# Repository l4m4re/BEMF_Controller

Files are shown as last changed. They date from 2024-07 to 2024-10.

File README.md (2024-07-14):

# BEMF Controller

The Back EMF Controller is an experimental evolution of the successful [EasyController3](https://github.com/pgrady3/EasyController3). 

This version incorporates an asymmetric bridge topology, which allows for capturing and reusing the energy from the motor's back EMF, which is normally wasted because of the use of freewheeling diodes.

This allows for a more efficient controller, and potentially a longer range for battery-powered applications, as explained on [Wikipedia](https://en.wikipedia.org/wiki/Switched_reluctance_motor#Power_circuitry):

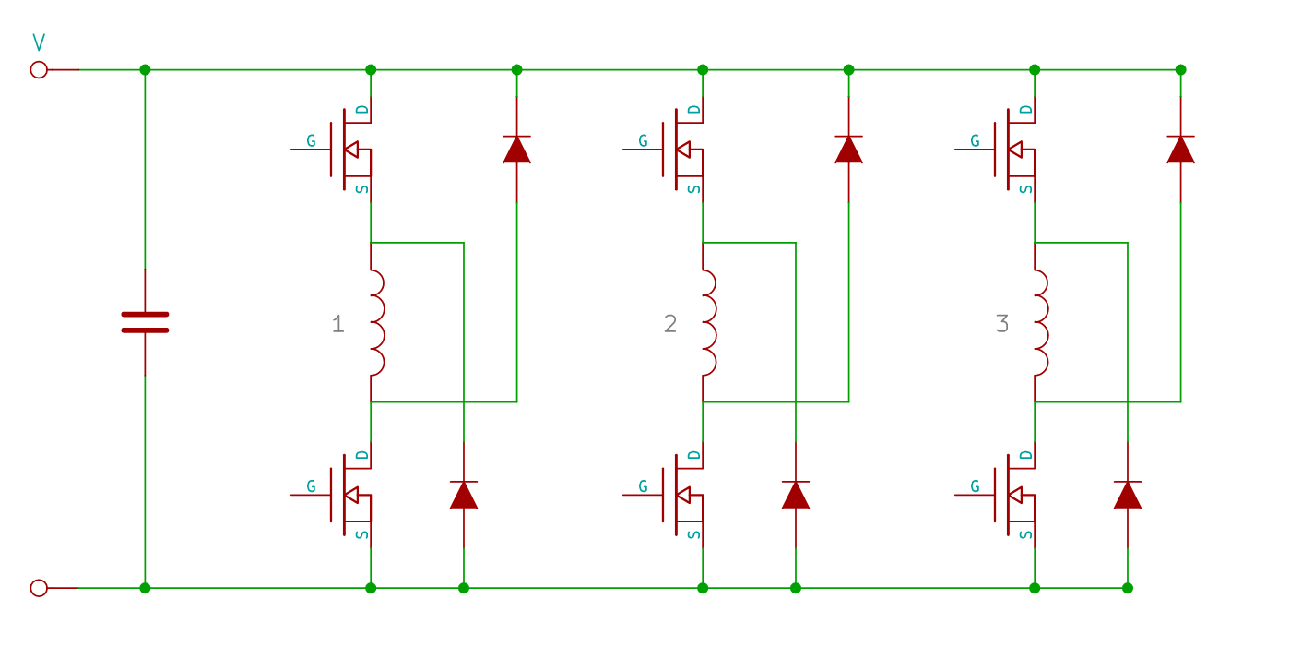
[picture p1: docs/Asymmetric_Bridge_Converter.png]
Asymmetric Bridge


> The phases in an asymmetric bridge converter correspond to the motor phases. If both of the power switches on either side of the phase are turned on, then that corresponding phase is actuated. Once the current has risen above the set value, the switch turns off. The energy now stored within the winding maintains the current in the same direction, the so-called back EMF (BEMF). This BEMF is fed back through the diodes to the capacitor for re-use, thus improving efficiency.

In addition to this, the capacitor that is used to store the energy from the back EMF is implemented in a bank of 4 capacitors, which are switched between series (BEMF capture) and parallel (coil energizing) by means of a couple of diodes:

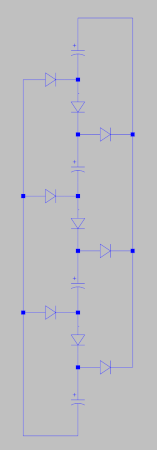
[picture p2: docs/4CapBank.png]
Capacitor Bank


[Spice simulations](http://tuks.nl/wiki/index.php/Main/BEMFRecoveryCircuit) have shown that this way the time needed to collapse the magnetic field in the motor is significantly reduced, which might help to reduce rotor drag and thus further improve the efficiency of the controller:

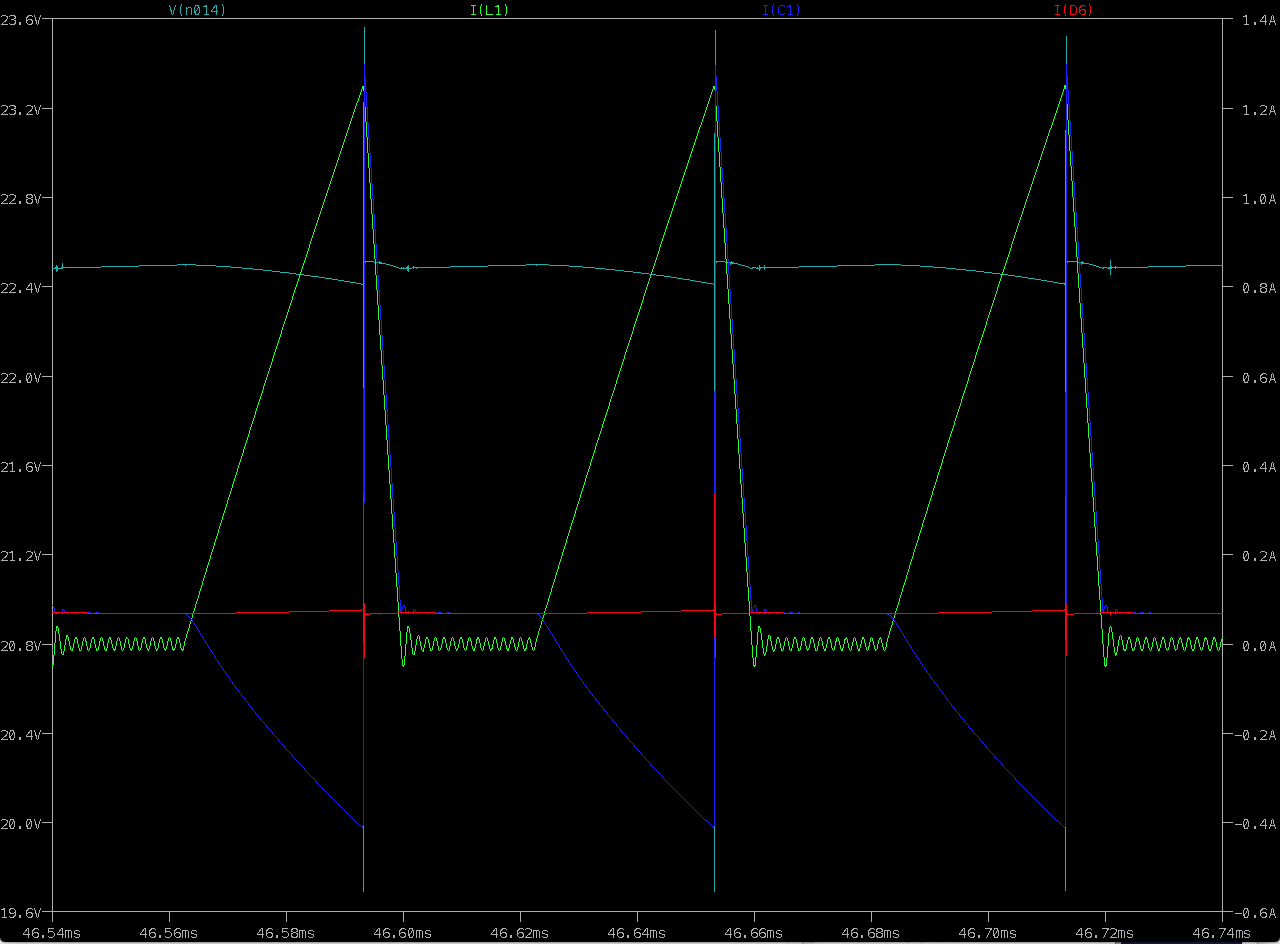
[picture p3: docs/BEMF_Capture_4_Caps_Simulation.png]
Spice simulation of 4 capacitor bank


At this moment, all of this is still a work in progress, and the controller is still in the design phase. 

## Schematic

At this moment, the schematic is being developed using KiCad, and can be found in the `kicad` folder. The schematic is still a work in progress, but the current version can be found [here](/kicad/BEMF_controller.pdf).

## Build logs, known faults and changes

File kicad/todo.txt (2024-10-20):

* Opamp buffers for Hall inputs -> check
* Finish buck converter -> check 
* Change gate drivers to LF2190NTR -> check
* Change trough hole resistors to smd -> check
* Change 10V charge pump to regulator
* Voltage sense now lower voltage and diodes no longer necessary since no cap switching
* Hall sensors could be DRV5055A3ELPGMQ1 https://www.digikey.nl/short/mpwrm95b 
* Connectors rather than pads -> ceck
* mounting holes
* check if inputs pen 1-4 can be used as digital inputs

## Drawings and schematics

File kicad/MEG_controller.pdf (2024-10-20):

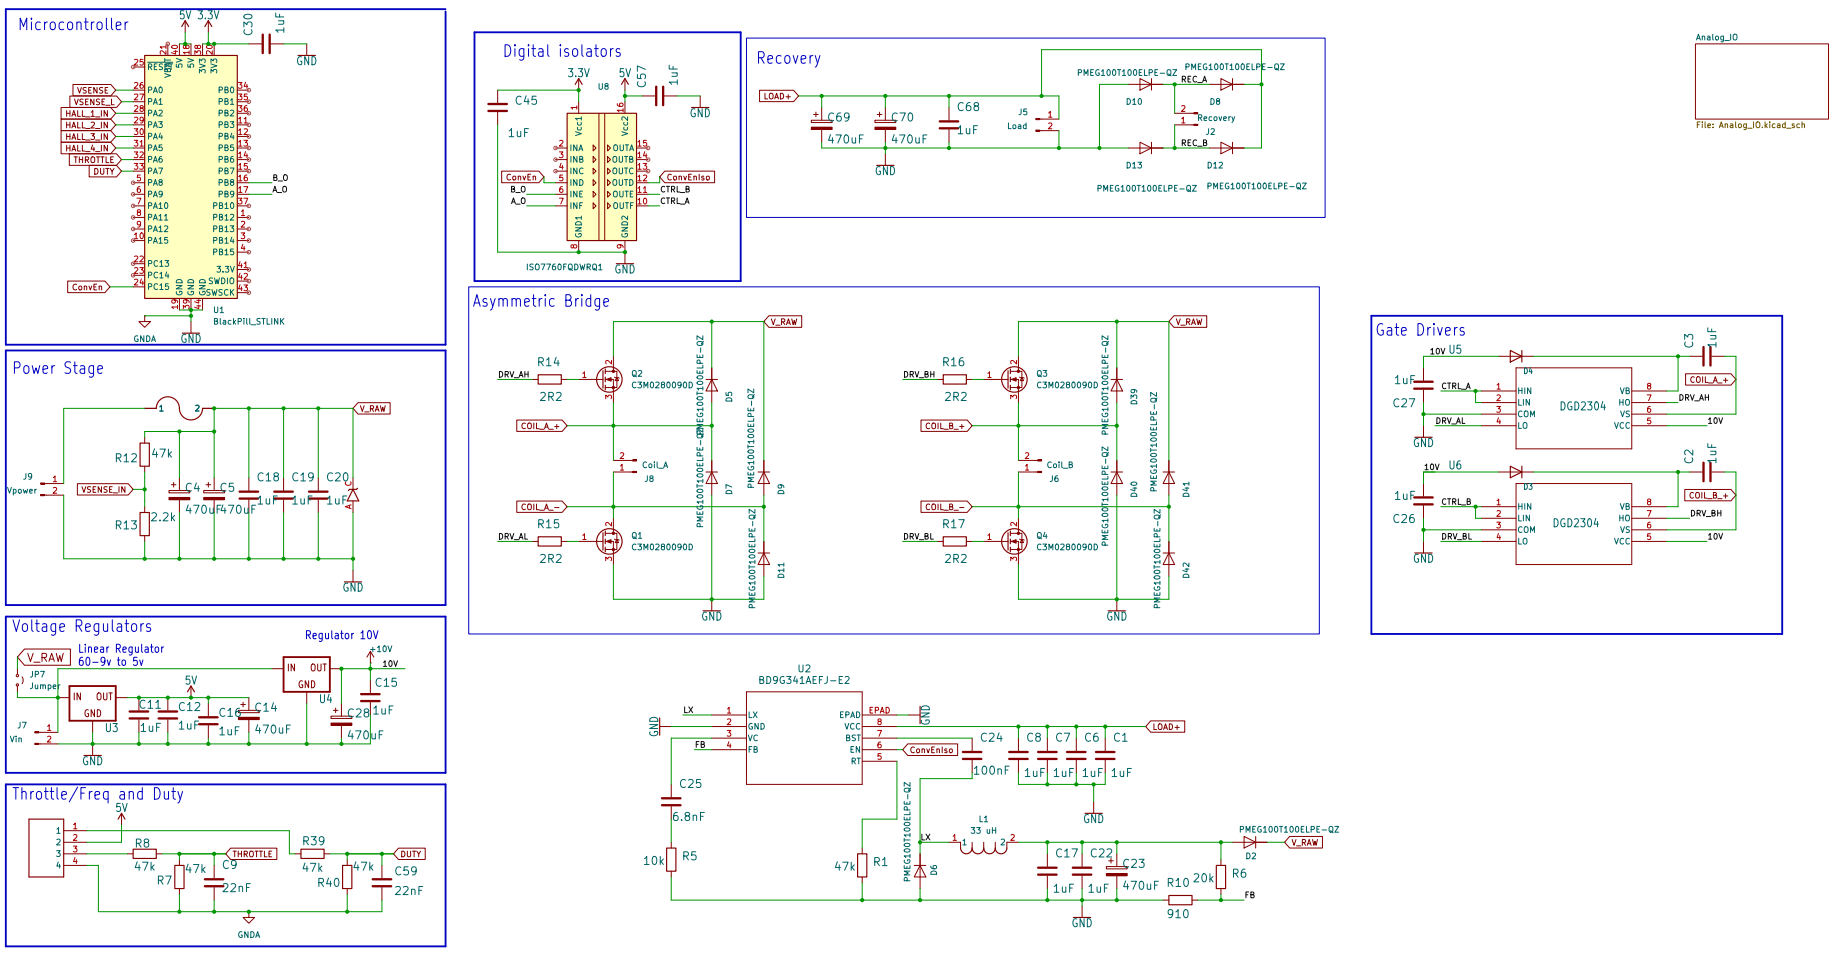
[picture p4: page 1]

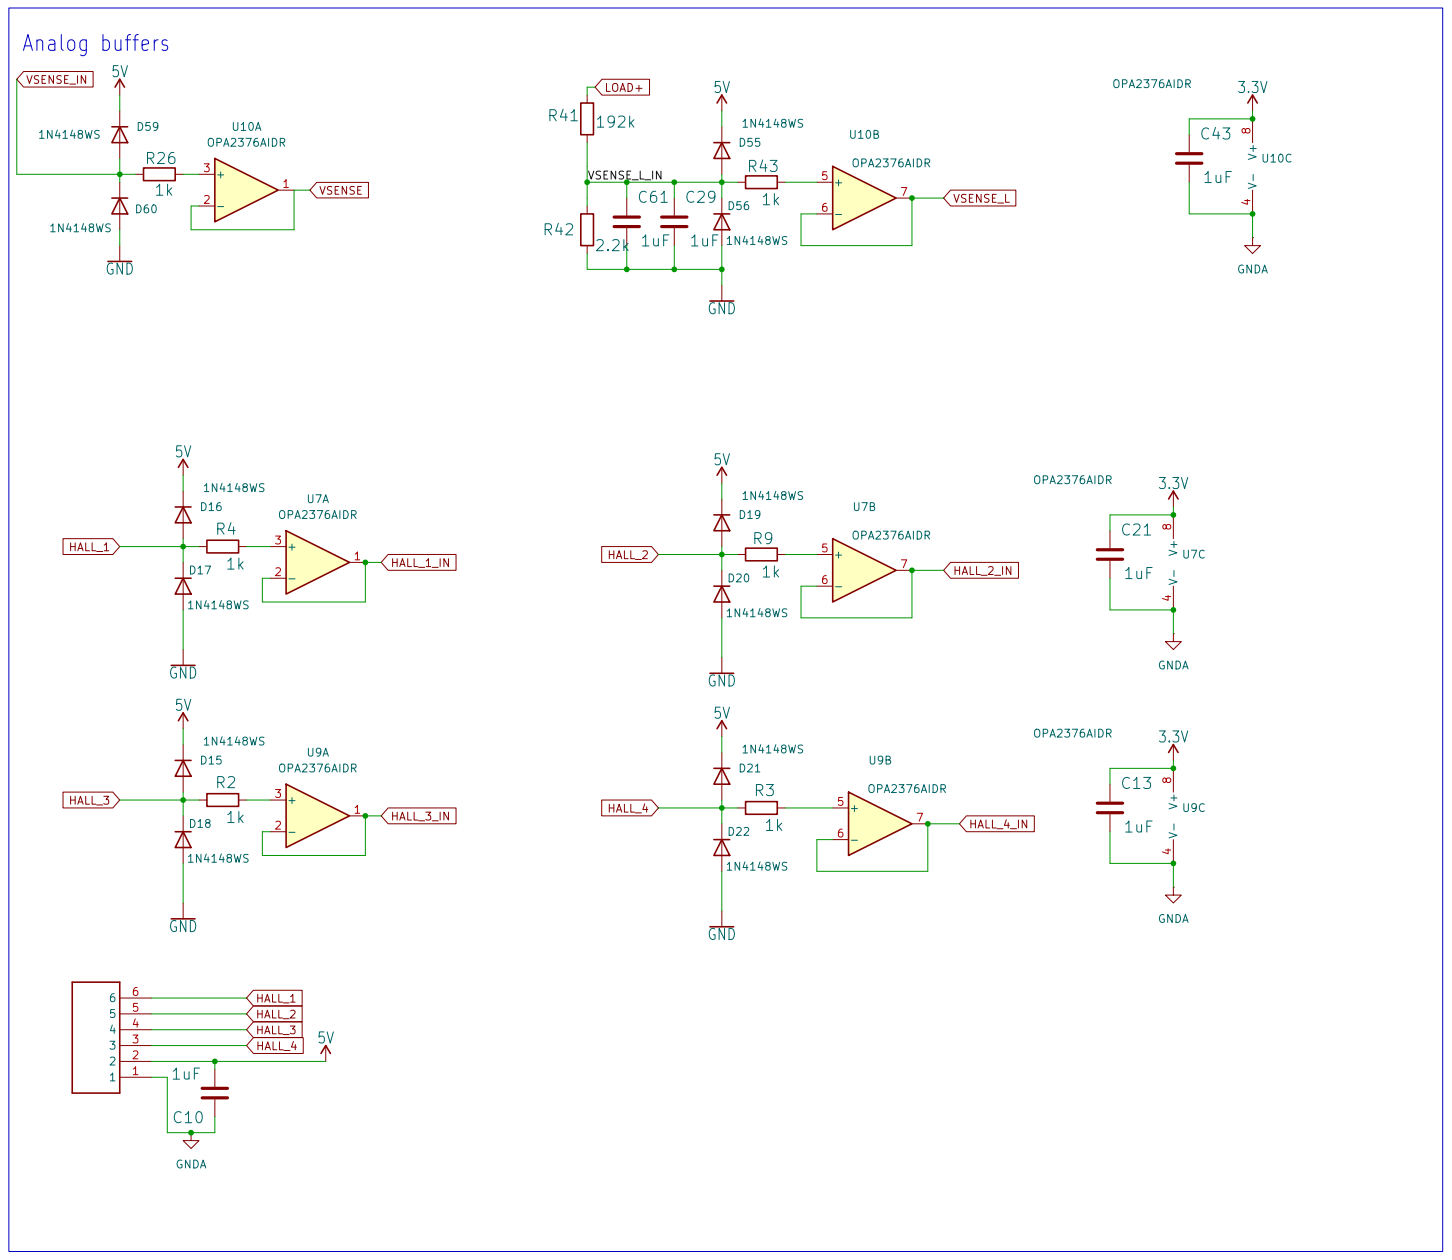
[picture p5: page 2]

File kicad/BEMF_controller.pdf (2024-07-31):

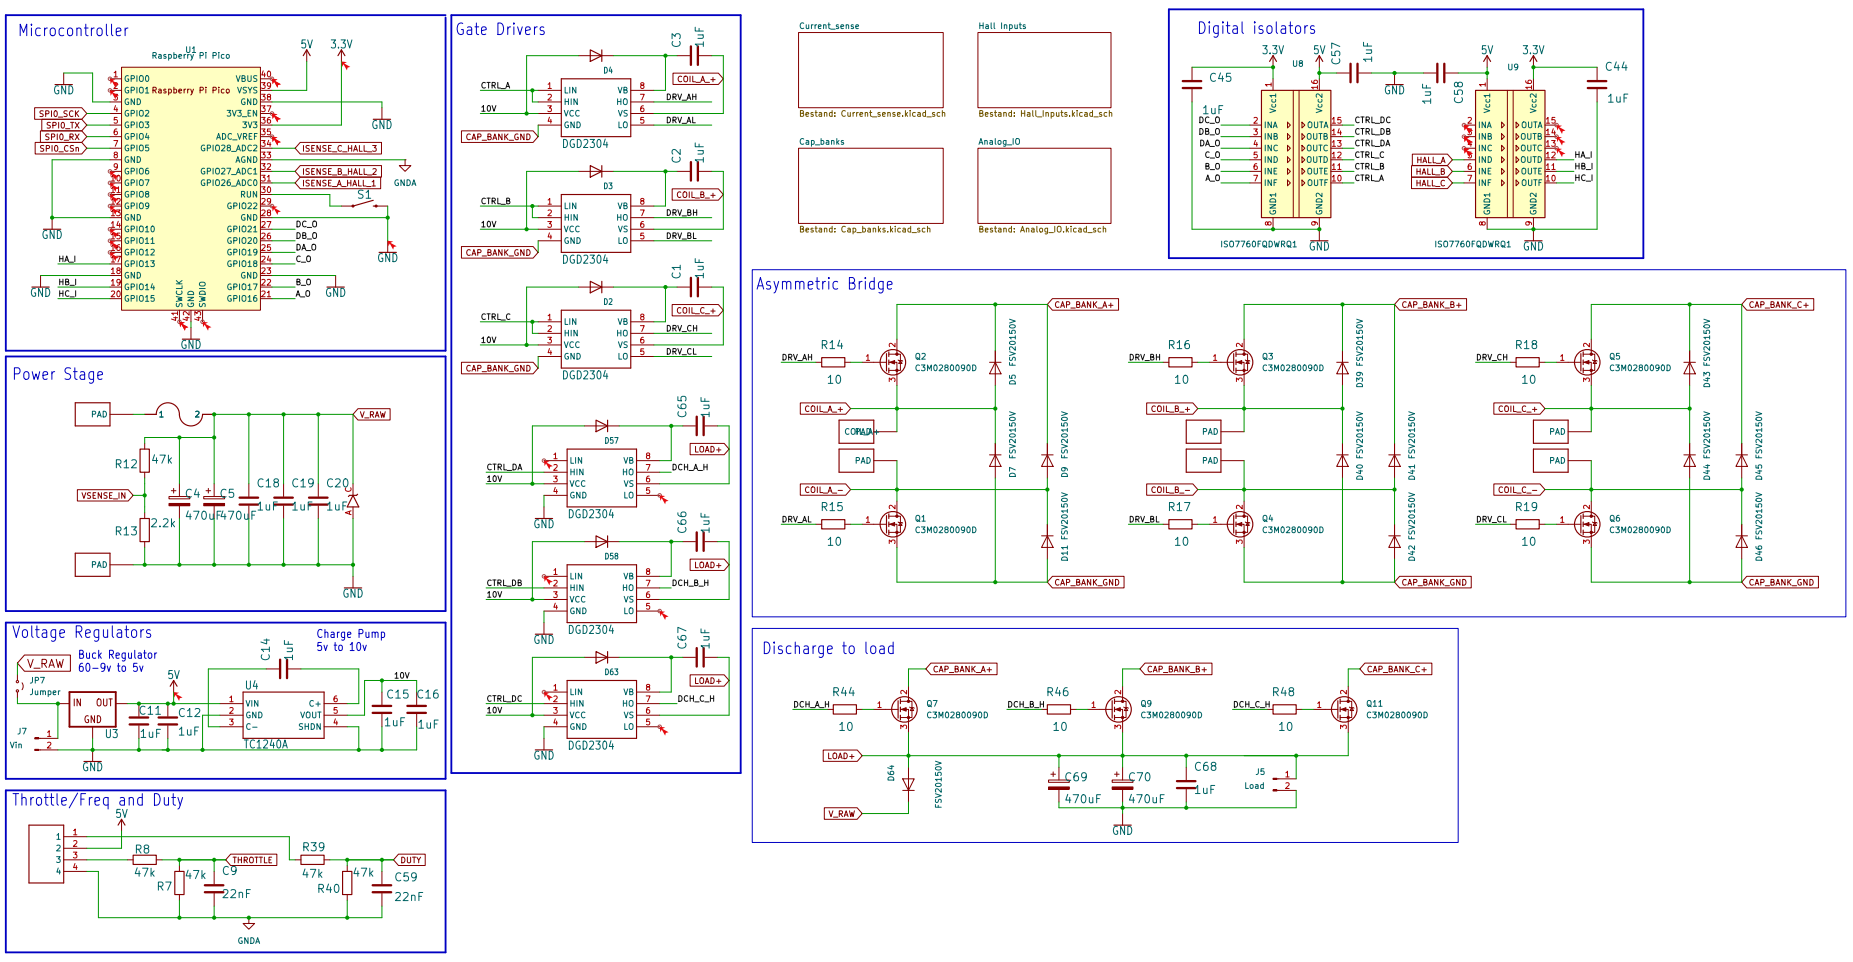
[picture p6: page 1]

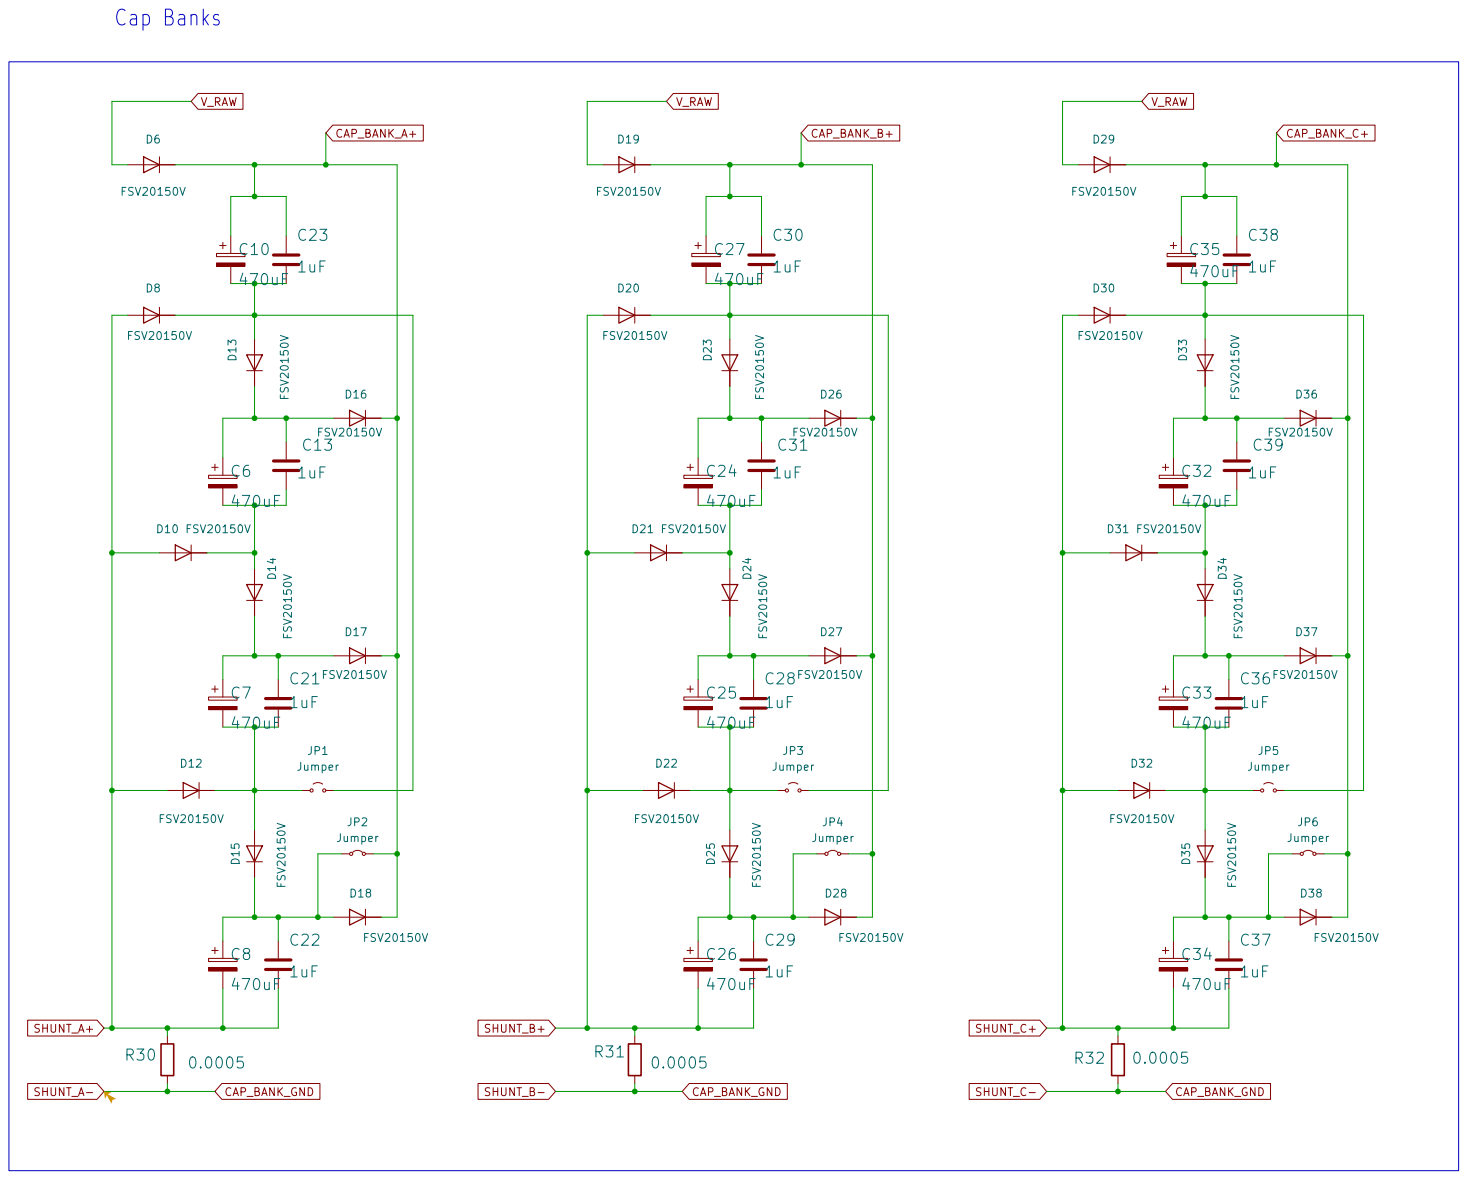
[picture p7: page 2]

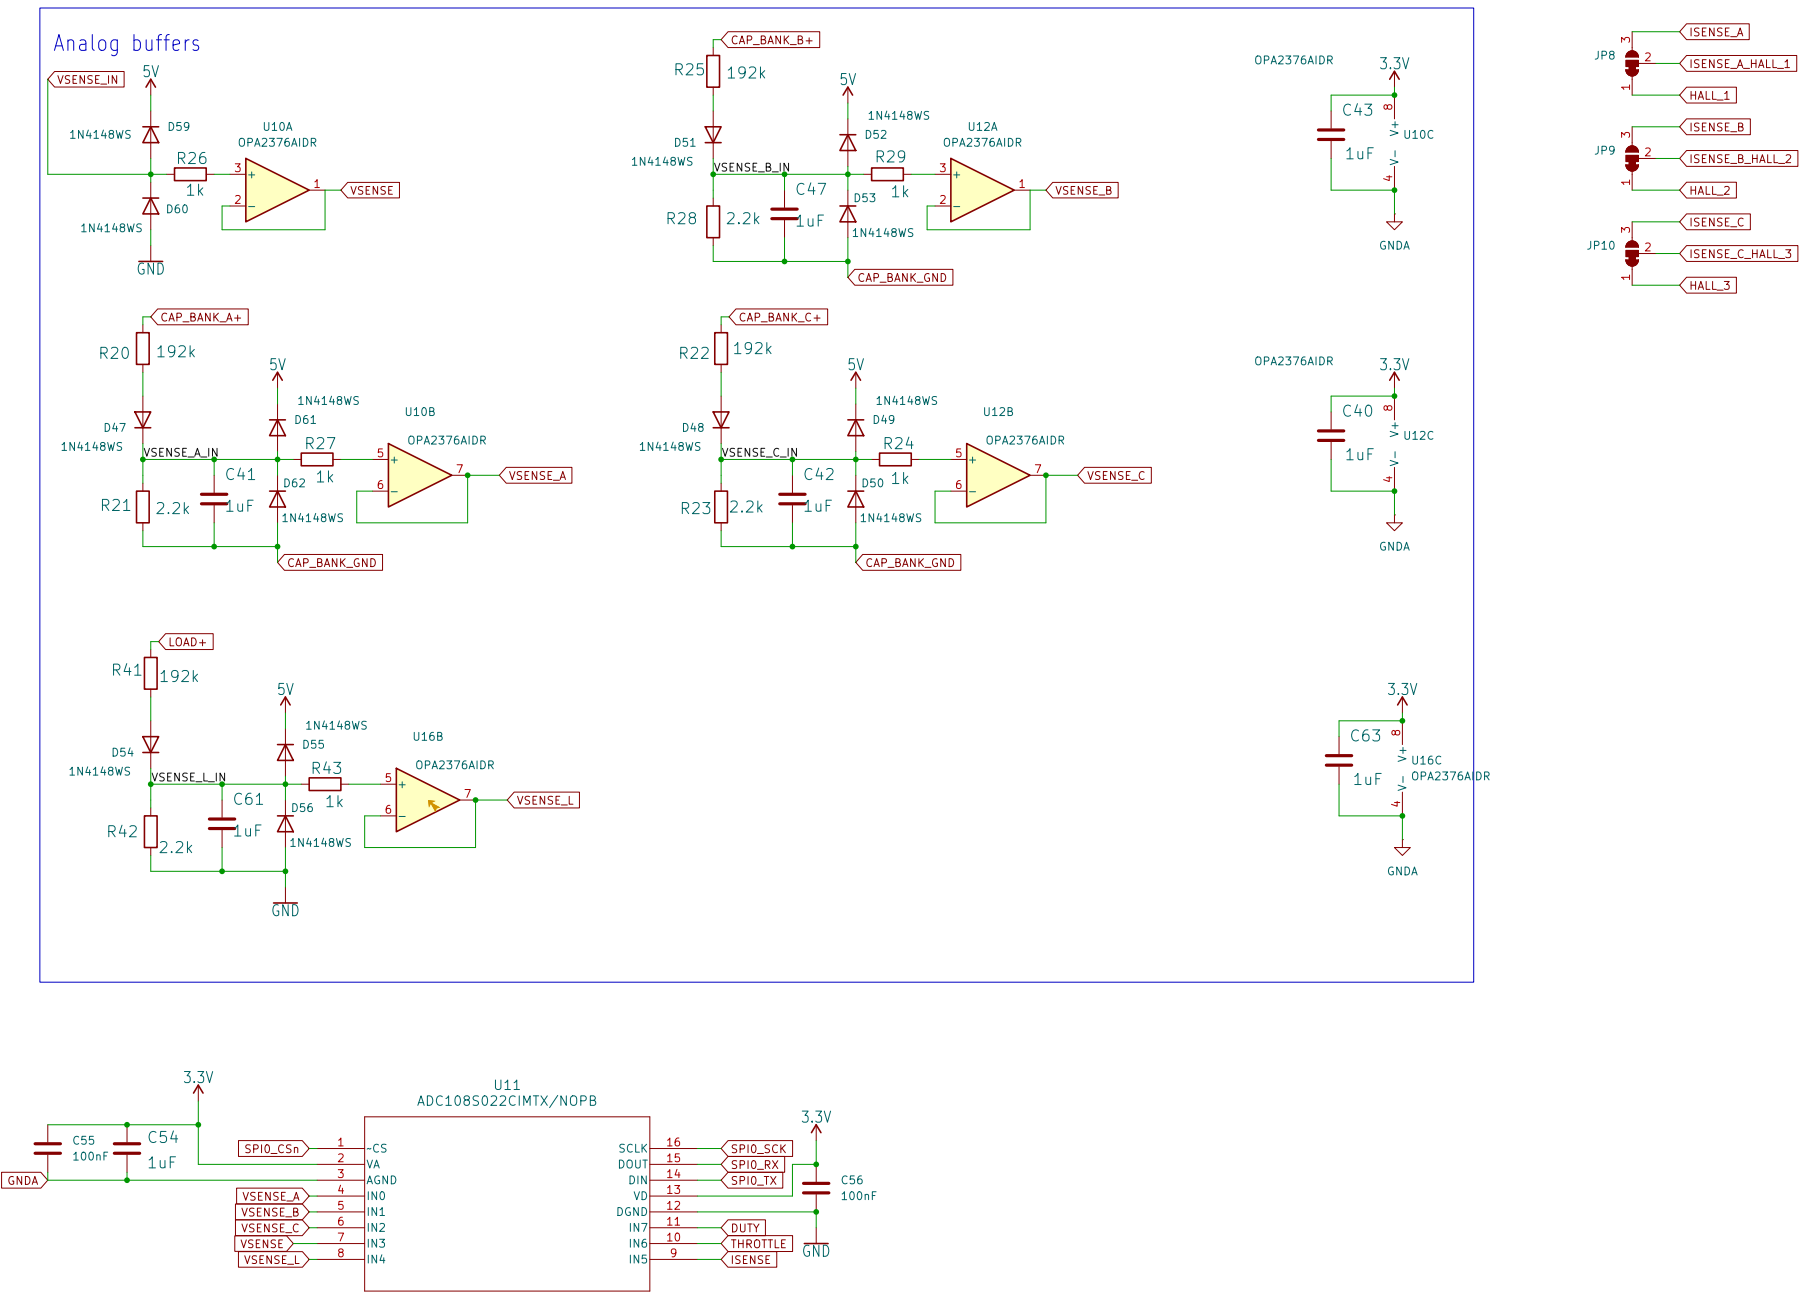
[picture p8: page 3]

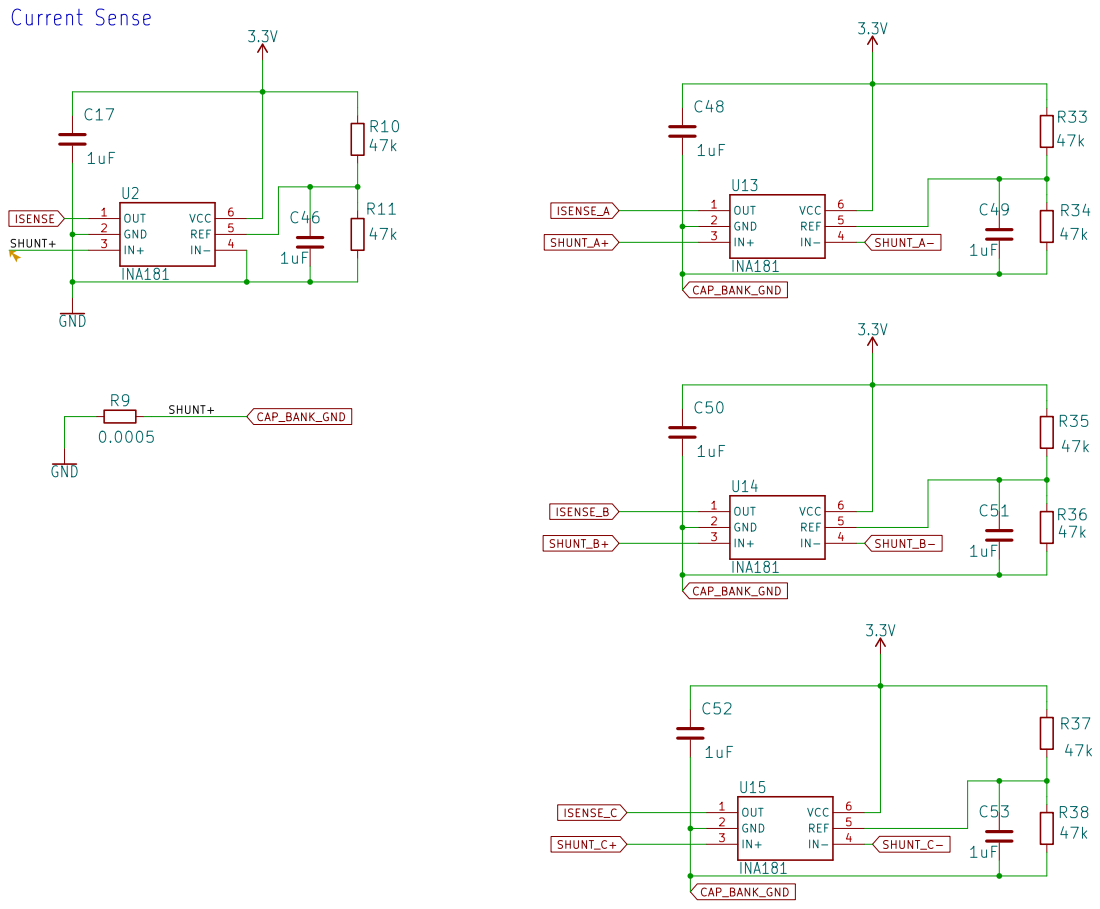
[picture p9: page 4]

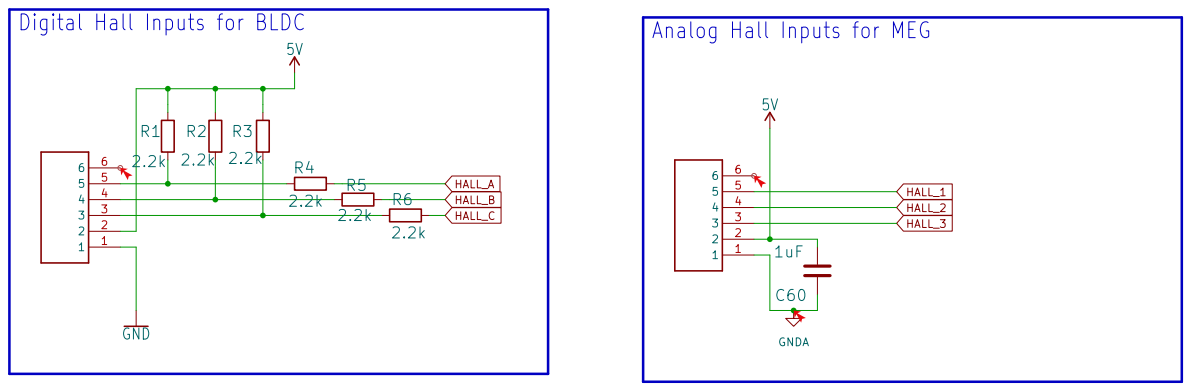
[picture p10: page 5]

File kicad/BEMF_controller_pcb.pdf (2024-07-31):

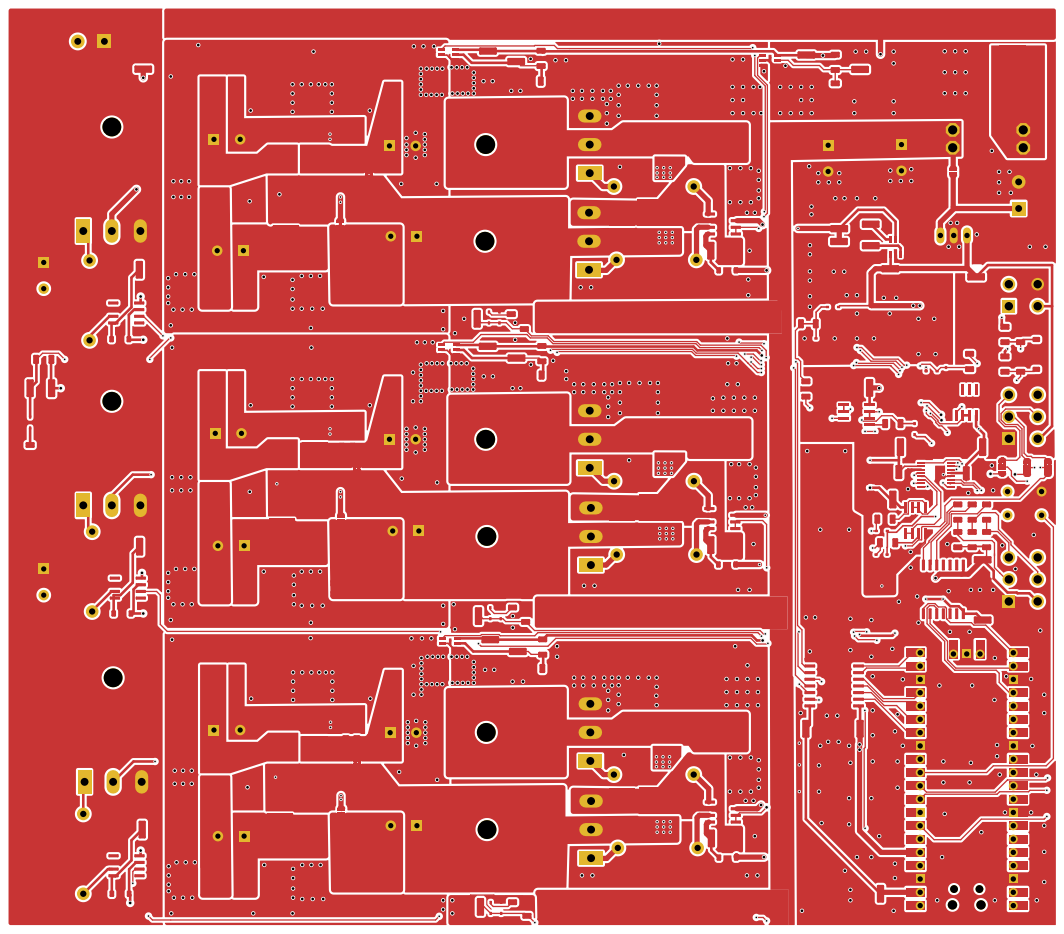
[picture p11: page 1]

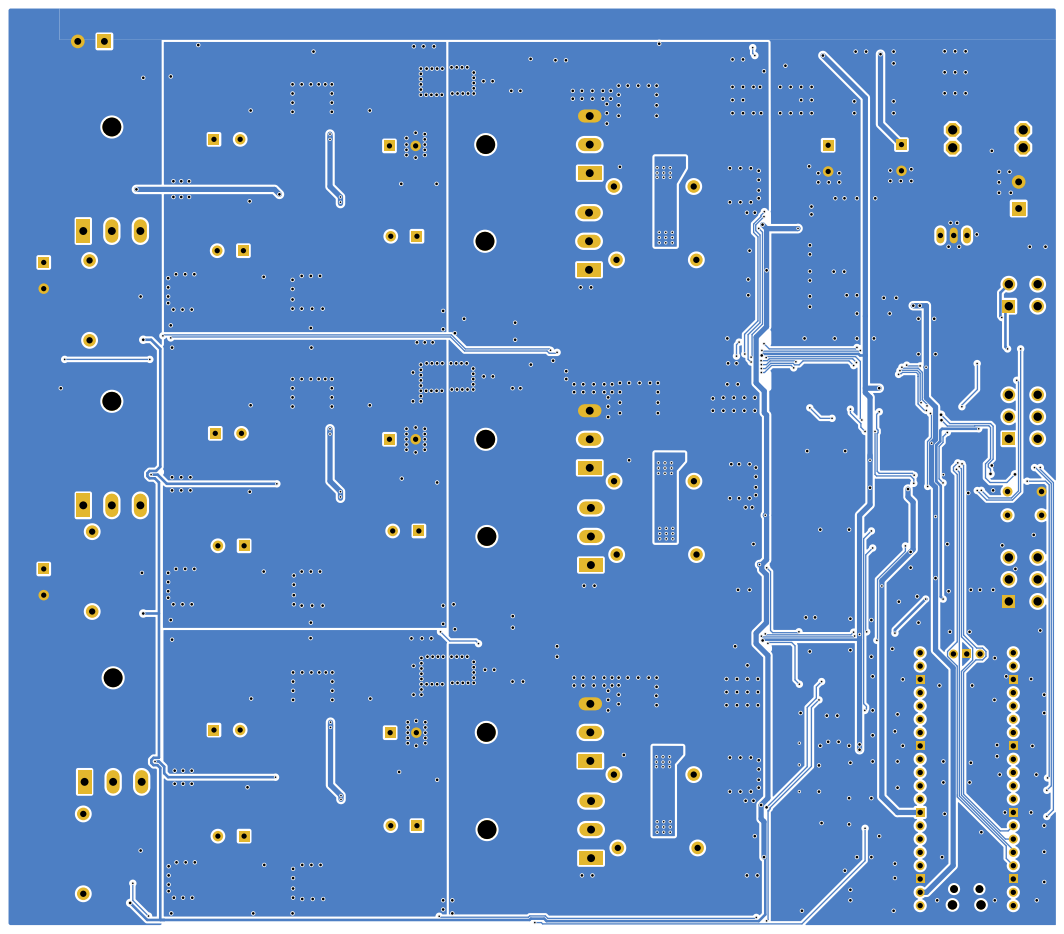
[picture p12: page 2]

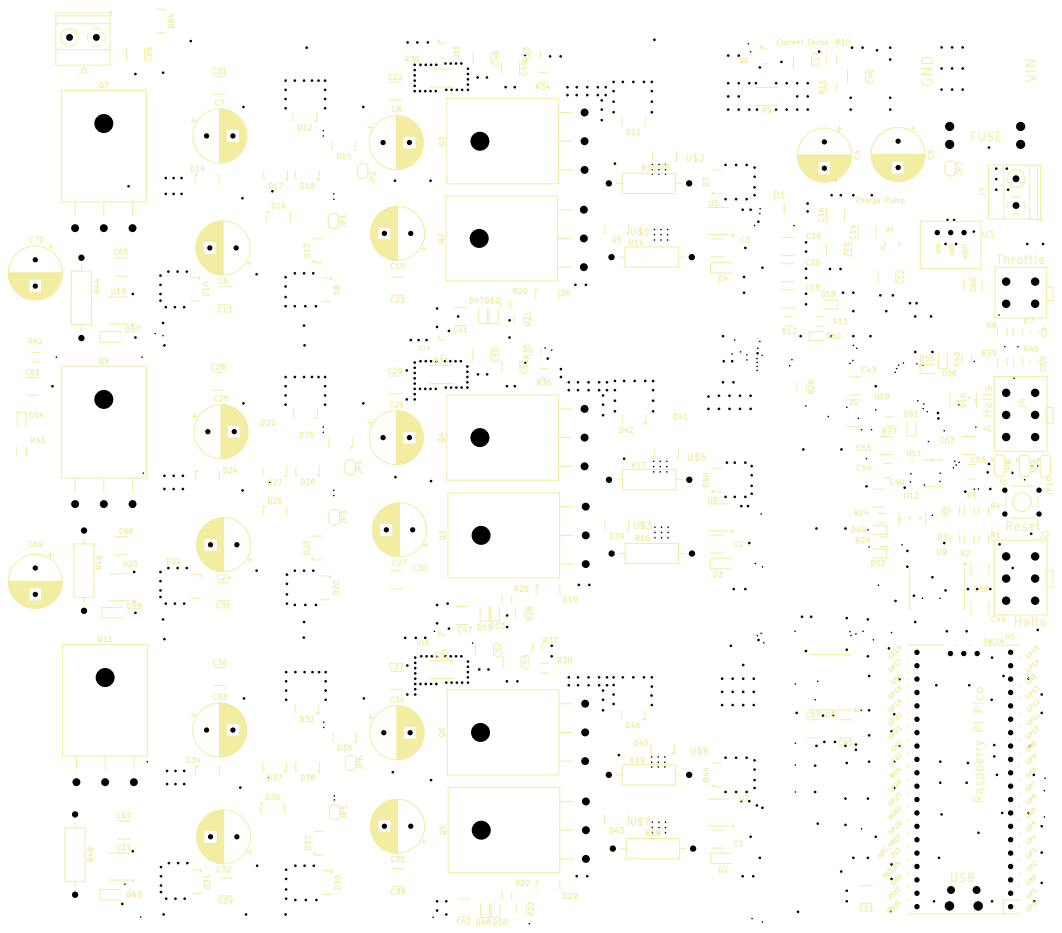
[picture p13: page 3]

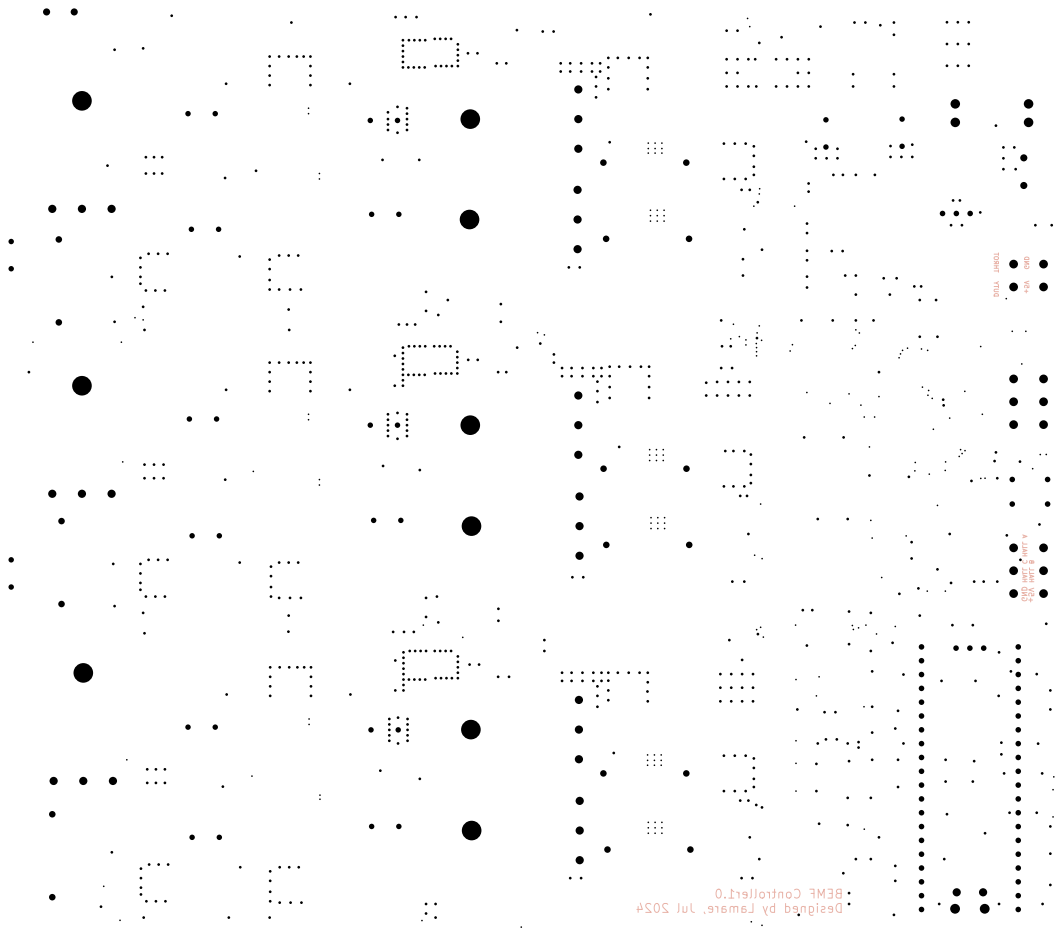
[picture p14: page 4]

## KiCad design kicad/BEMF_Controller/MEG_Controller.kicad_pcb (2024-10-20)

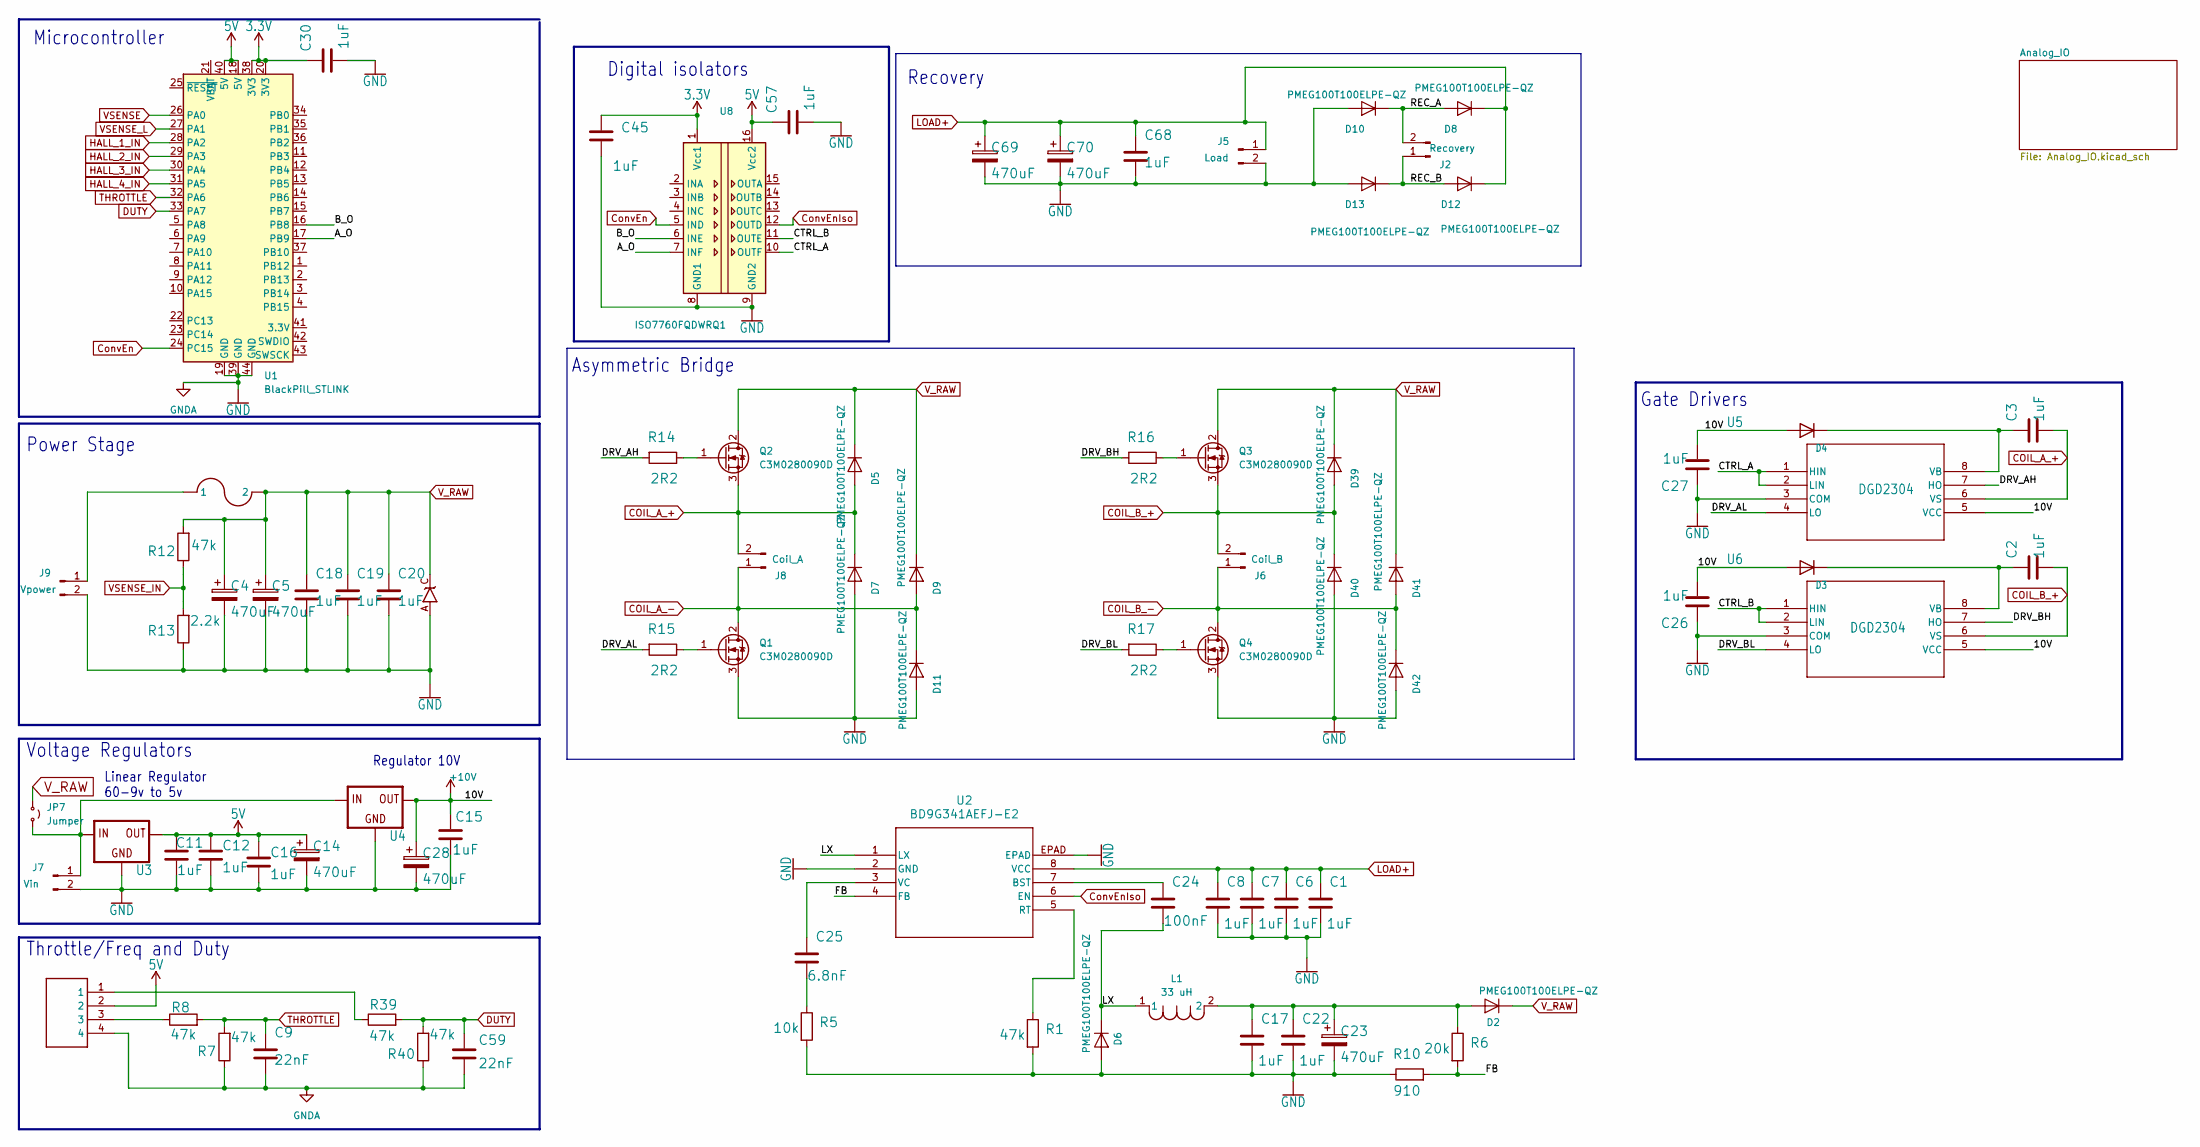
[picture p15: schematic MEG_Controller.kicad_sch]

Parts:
C1, C2, C3, C6, C7, C8, C11, C12, C15, C16, C17, C18, C19, C20, C22, C26, C27, C30, C45, C57, C68: 1uF; C_1812_4532Metric
C4, C5, C14, C23, C28, C69, C70: 470uF; CP_Radial_D10.0mm_P5.00mm
C9, C59: 22nF; C_0805_2012Metric
C24: 100nF; C_0805_2012Metric
C25: 6.8nF; C_0805_2012Metric
D1: TVS_UNIDO-214AC; DO-214AC
D2, D5, D6, D7, D8, D9, D10, D11, D12, D13, D39, D40, D41, D42: PMEG100T100ELPE-QZ; Nexperia_CFP15_SOT-1289
D3, D4: SMD-DIODE-100V-200MA(SOD-123); D_SOD-123
J1: HEADER4VALULOK; TerminalBlock_Phoenix_MKDS-1,5-4-5.08_1x04_P5.08mm_Horizont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
J2: Recovery; TerminalBlock_Phoenix_MKDS-1,5-2-5.08_1x02_P5.08mm_Horizont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
J3: FUSE; AUTO_FUSE
J5: Load; TerminalBlock_Phoenix_MKDS-1,5-2-5.08_1x02_P5.08mm_Horizont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
J6: Coil_B; TerminalBlock_Phoenix_MKDS-1,5-2-5.08_1x02_P5.08mm_Horizont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
J7: Vin; TerminalBlock_Phoenix_MKDS-1,5-2-5.08_1x02_P5.08mm_Horizont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
J8: Coil_A; TerminalBlock_Phoenix_MKDS-1,5-2-5.08_1x02_P5.08mm_Horizont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
J9: Vpower; TerminalBlock_Phoenix_MKDS-1,5-2-5.08_1x02_P5.08mm_Horizont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
JP7: Jumper; SolderJumper-2_P1.3mm_Open_RoundedPad1.0x1.5mm
L1: 33 uH; IND_BOURNS_SRN1060
Q1, Q2, Q3, Q4: C3M0280090D; TO-247-3_Vertical
R1, R7, R8, R12, R39, R40: 47k; R_1206_3216Metric
R5: 10k; R_1206_3216Metric
R6: 20k; R_1206_3216Metric
R10: 910; R_1206_3216Metric
R13: 2.2k; R_1206_3216Metric
R14, R15, R16, R17: 2R2; R_1206_3216Metric
U1: BlackPill_STLINK
U2: BD9G341AEFJ-E2; HTSOP-J8_ROM
U3: V_REG_7805; V78W_BACKWARDS
U4: V_REG_7810; V78W_BACKWARDS
U5, U6: DGD2304; SOICN-8_LTF
U8: ISO7760FQDWRQ1; SOIC-16W_7.5x10.3mm_P1.27mm

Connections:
3.3V: C30.1, C45.1, U1.20 (3V3), U1.38 (3V3), U8.1 (Vcc1); also elsewhere on the board
5V: C11.1, C12.1, C14.1, C16.1, C57.1, J1.2, U1.18 (5V), U1.40 (5V), U3.OUT, U8.16 (Vcc2); also elsewhere on the board
+10V: C15.1, C26.2, C27.2, C28.1, D3.2 (A), D4.2 (A), U4.OUT, U5.5 (VCC), U6.5 (VCC)
/A_O: U1.17 (PB9), U8.7 (INF)
/B_O: U1.16 (PB8), U8.6 (INE)
/CTRL_A: U5.1 (HIN), U5.2 (LIN), U8.10 (OUTF)
/CTRL_B: U6.1 (HIN), U6.2 (LIN), U8.11 (OUTE)
/DRV_AH: R14.2, U5.7 (HO)
/DRV_AL: R15.2, U5.4 (LO)
/DRV_BH: R16.2, U6.7 (HO)
/DRV_BL: R17.2, U6.4 (LO)
/FB: R6.2, R10.2, U2.4 (FB)
/LX: C24.2, D6.1 (A), D6.2 (A), L1.1, U2.1 (LX)
/REC_A: D8.3 (K), D10.1 (A), D10.2 (A), J2.2
/REC_B: D12.3 (K), D13.1 (A), D13.2 (A), J2.1
COIL_A_+: C3.2, D5.3 (K), D7.1 (A), D7.2 (A), J8.2, Q2.3 (S), U5.6 (VS)
COIL_A_-: D9.3 (K), D11.1 (A), D11.2 (A), J8.1, Q1.2 (D)
COIL_B_+: C2.2, D39.3 (K), D40.1 (A), D40.2 (A), J6.2, Q3.3 (S), U6.6 (VS)
COIL_B_-: D41.3 (K), D42.1 (A), D42.2 (A), J6.1, Q4.2 (D)
ConvEn: U1.24 (PC15), U8.5 (IND)
ConvEnIso: U2.6 (EN), U8.12 (OUTD)
DUTY: C59.1, R39.2, R40.2, U1.33 (PA7)
GND: C1.2, C4.2, C5.2, C6.2, C7.2, C8.2, C9.2, C11.2, C12.2, C14.2, C15.2, C16.2, C17.2, C18.2, C19.2, C20.2, C22.2, C23.2, C26.1, C27.1, C28.2, C30.2, C45.2, C57.2, C59.2, C68.2, C69.2, C70.2, D1.A, D6.3 (K), D7.3 (K), D10.3 (K), D11.3 (K), D13.3 (K), D40.3 (K), D42.3 (K), J1.4, J5.2, J7.2, J9.2, Q1.3 (S), Q4.3 (S), R1.2, R5.2, R7.1, R10.1, R13.1, R40.1, U1.19 (GND), U1.39 (GND), U1.44 (GND), U2.2 (GND), U2.EPAD, U3.GND, U4.GND, U5.3 (COM), U6.3 (COM), U8.8 (GND1), U8.9 (GND2); also elsewhere on the board
HALL_1_IN: U1.28 (PA2); also elsewhere on the board
HALL_2_IN: U1.29 (PA3); also elsewhere on the board
HALL_3_IN: U1.30 (PA4); also elsewhere on the board
HALL_4_IN: U1.31 (PA5); also elsewhere on the board
LOAD+: C1.1, C6.1, C7.1, C8.1, C68.1, C69.1, C70.1, D8.1 (A), D8.2 (A), D12.1 (A), D12.2 (A), J5.1, U2.8 (VCC); also elsewhere on the board
unnamed: C25.2, R5.1
unnamed: C17.1, C22.1, C23.1, D2.3 (K), L1.2, R6.1
unnamed: C2.1, D3.1 (K), U6.8 (VB)
unnamed: C3.1, D4.1 (K), U5.8 (VB)
unnamed: J1.1, R39.1
unnamed: J1.3, R8.1
unnamed: J7.1, JP7.2 (B), U3.IN, U4.IN
unnamed: J3.1A (1), J3.1B (1), J9.1
unnamed: Q1.1 (G), R15.1
unnamed: Q2.1 (G), R14.1
unnamed: Q3.1 (G), R16.1
unnamed: Q4.1 (G), R17.1
unnamed: C24.1, U2.7 (BST)
unnamed: R1.1, U2.5 (RT)
unnamed: C25.1, U2.3 (VC)
THROTTLE: C9.1, R7.2, R8.2, U1.32 (PA6)
VSENSE: U1.26 (PA0); also elsewhere on the board
VSENSE_IN: R12.1, R13.2; also elsewhere on the board
VSENSE_L: U1.27 (PA1); also elsewhere on the board
V_RAW: C4.1, C5.1, C18.1, C19.1, C20.1, D1.C, D2.1 (A), D2.2 (A), D5.1 (A), D5.2 (A), D9.1 (A), D9.2 (A), D39.1 (A), D39.2 (A), D41.1 (A), D41.2 (A), J3.2A (2), J3.2B (2), JP7.1 (A), Q2.2 (D), Q3.2 (D), R12.2

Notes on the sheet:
Digital isolators
Power Stage
Throttle/Freq and Duty
Microcontroller
Regulator 10V
Linear Regulator 60-9v to 5v
Voltage Regulators
Gate Drivers
Recovery
Asymmetric Bridge

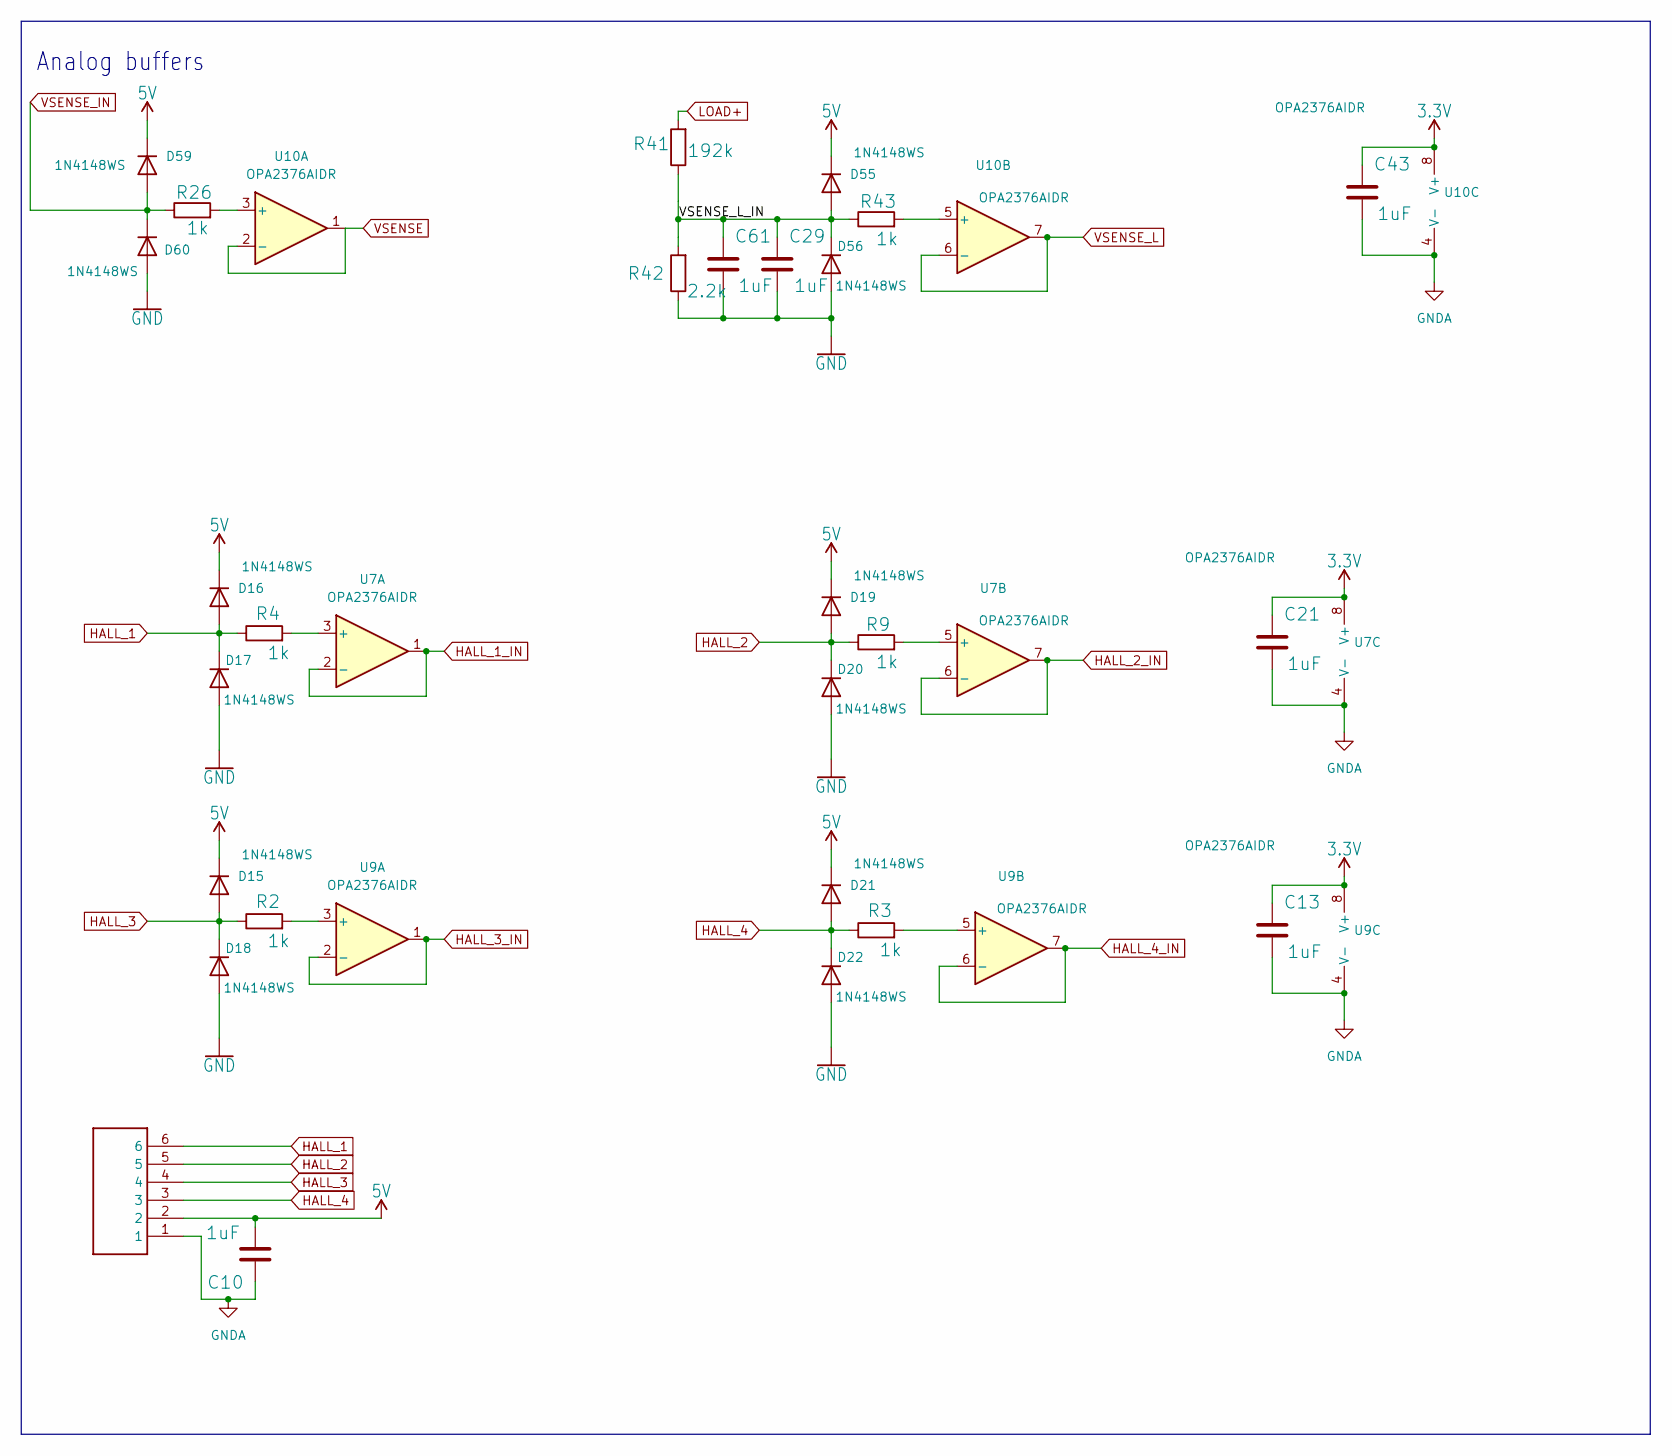
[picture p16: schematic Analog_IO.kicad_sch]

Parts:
C10, C13, C21, C29, C43, C61: 1uF; C_1812_4532Metric
D15, D16, D17, D18, D19, D20, D21, D22, D55, D56, D59, D60: 1N4148WS; D_SOD-323
J4: HEADER6; TerminalBlock_Phoenix_MKDS-1,5-6_1x06_P5.00mm_Horizontal
R2, R3, R4, R9, R26, R43: 1k; R_1206_3216Metric
R41: 192k; R_1206_3216Metric
R42: 2.2k; R_1206_3216Metric
U7, U9, U10: OPA2376AIDR; D8

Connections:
3.3V: C13.1, C21.1, C43.1, U7.8 (V+), U9.8 (V+), U10.8 (V+); also elsewhere on the board
5V: C10.2, D15.1 (K), D16.1 (K), D19.1 (K), D21.1 (K), D55.1 (K), D59.1 (K), J4.2; also elsewhere on the board
/Analog_IO/VSENSE_L_IN: C29.1, C61.1, D55.2 (A), D56.1 (K), R41.1, R42.2, R43.1
GND: C10.1, C13.2, C21.2, C29.2, C43.2, C61.2, D17.2 (A), D18.2 (A), D20.2 (A), D22.2 (A), D56.2 (A), D60.2 (A), J4.1, R42.1, U7.4 (V-), U9.4 (V-), U10.4 (V-); also elsewhere on the board
HALL_1: D16.2 (A), D17.1 (K), J4.6, R4.1
HALL_1_IN: U7.1, U7.2 (-); also elsewhere on the board
HALL_2: D19.2 (A), D20.1 (K), J4.5, R9.1
HALL_2_IN: U7.6 (-), U7.7; also elsewhere on the board
HALL_3: D15.2 (A), D18.1 (K), J4.4, R2.1
HALL_3_IN: U9.1, U9.2 (-); also elsewhere on the board
HALL_4: D21.2 (A), D22.1 (K), J4.3, R3.1
HALL_4_IN: U9.6 (-), U9.7; also elsewhere on the board
LOAD+: R41.2; also elsewhere on the board
unnamed: R4.2, U7.3 (+)
unnamed: R9.2, U7.5 (+)
unnamed: R2.2, U9.3 (+)
unnamed: R3.2, U9.5 (+)
unnamed: R26.2, U10.3 (+)
unnamed: R43.2, U10.5 (+)
VSENSE: U10.1, U10.2 (-); also elsewhere on the board
VSENSE_IN: D59.2 (A), D60.1 (K), R26.1; also elsewhere on the board
VSENSE_L: U10.6 (-), U10.7; also elsewhere on the board

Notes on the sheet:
Analog buffers

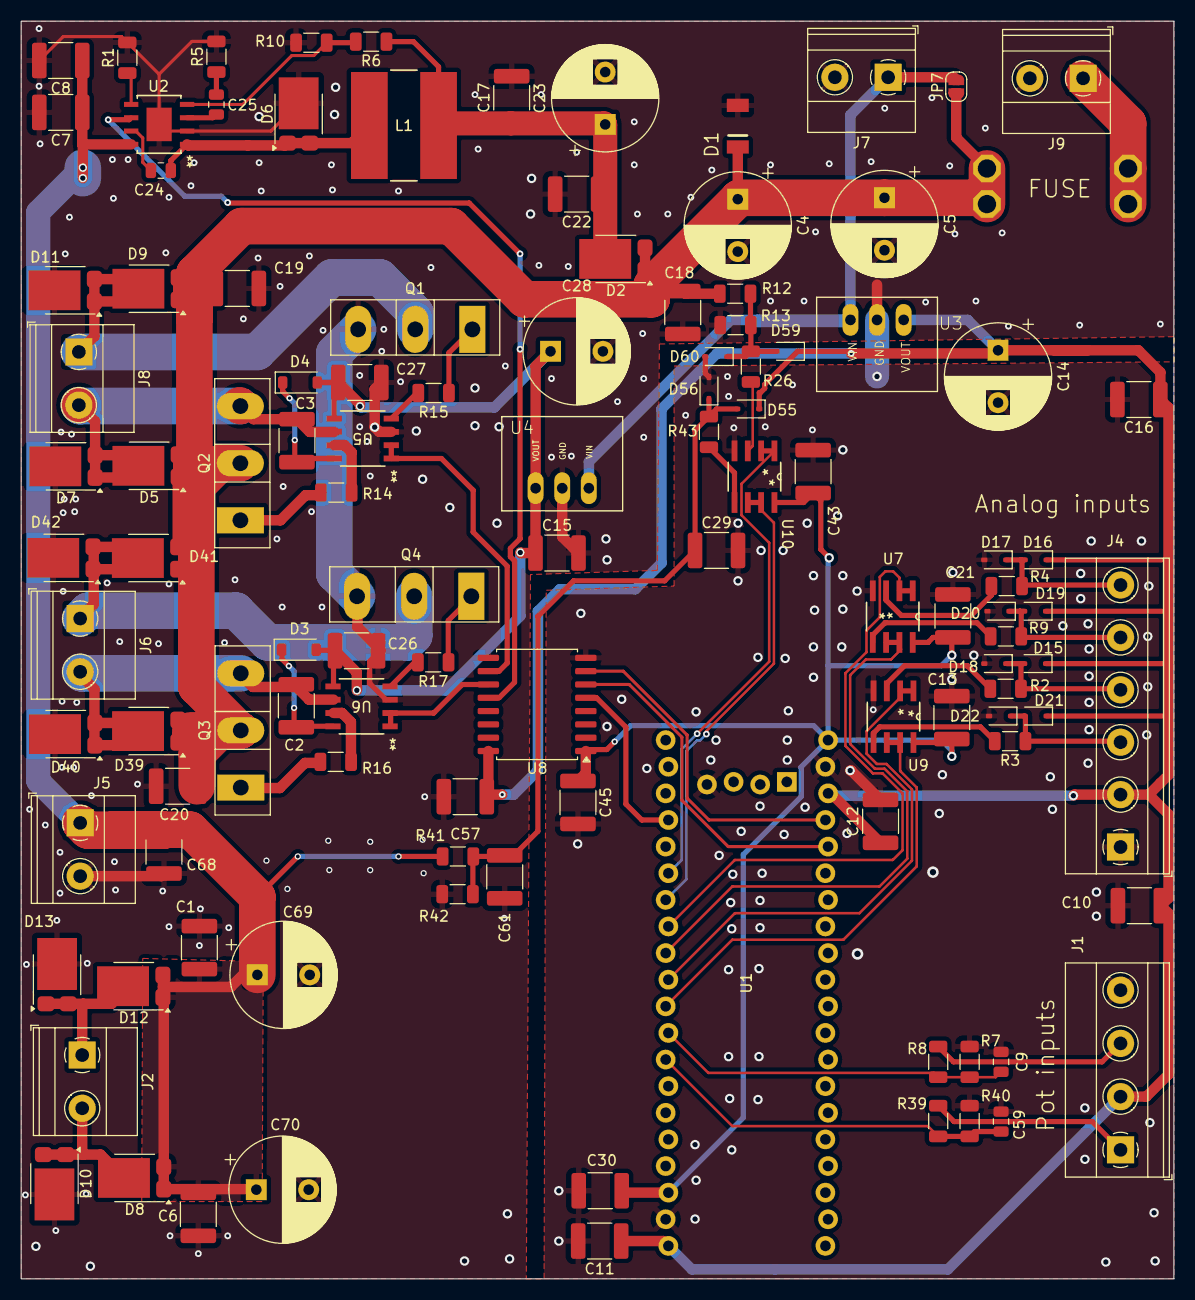
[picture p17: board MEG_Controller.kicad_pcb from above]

Board: 2 copper layers, 110.0 x 120.0 mm, 114 parts (0 on the bottom side), 59 nets.

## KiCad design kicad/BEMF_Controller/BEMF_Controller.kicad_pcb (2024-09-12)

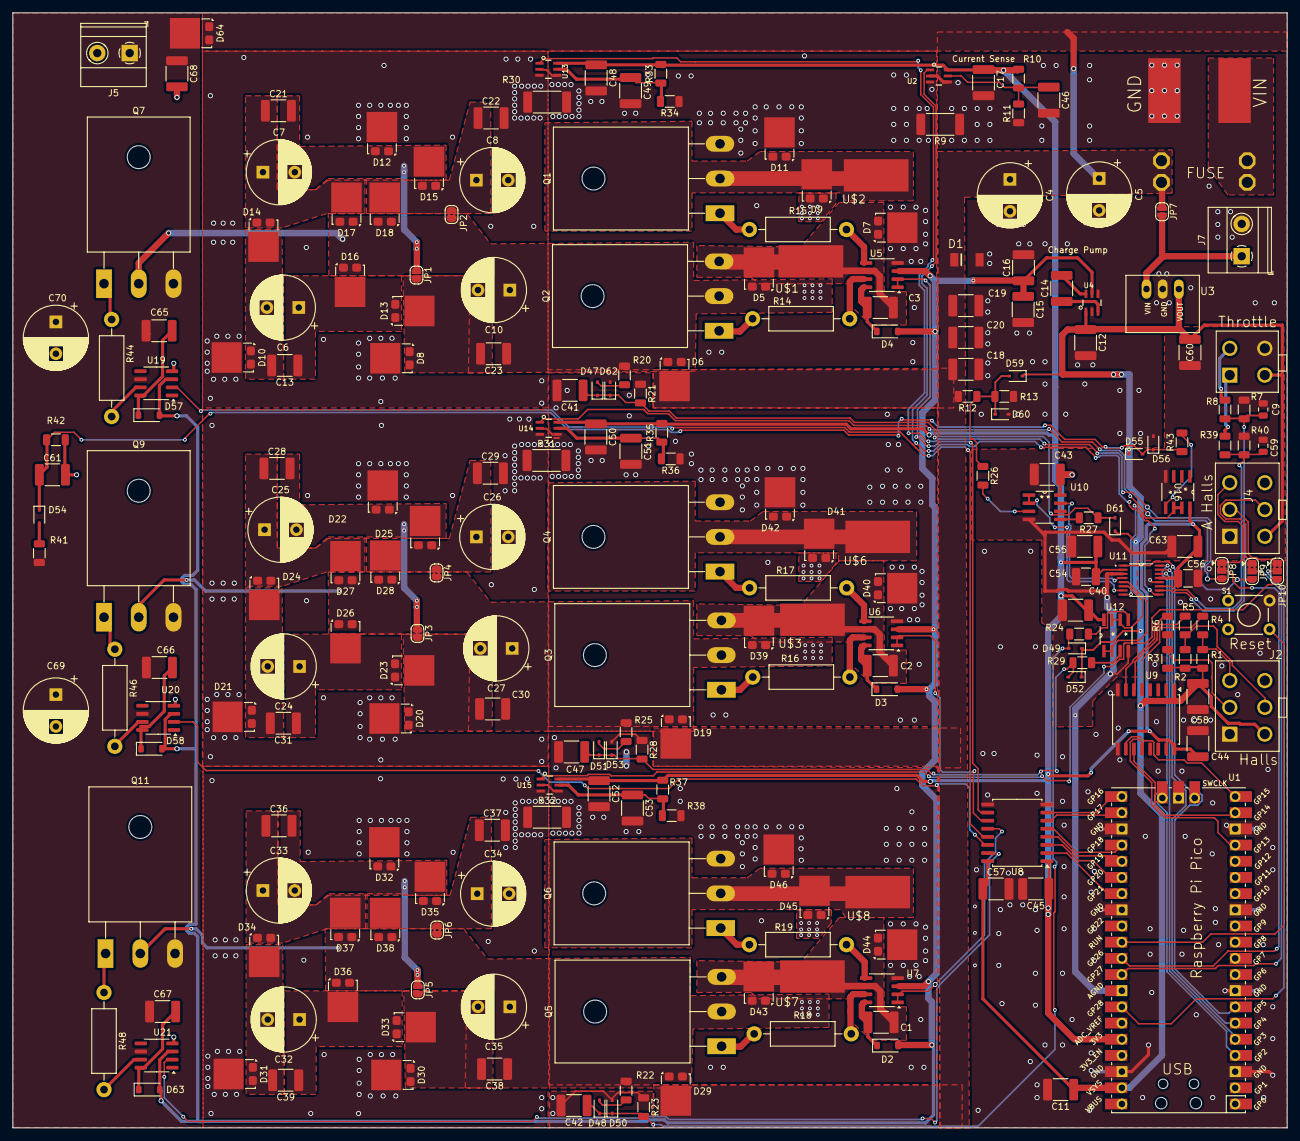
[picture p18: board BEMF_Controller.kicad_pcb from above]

Board: 2 copper layers, 200.0 x 175.0 mm, 231 parts (0 on the bottom side), 129 nets.

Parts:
C1, C2, C3, C11, C12, C13, C14, C15, C16, C17, C18, C19, C20, C21, C22, C23, C28, C29, C30, C31, C36, C37, C38, C39, C40, C41, C42, C43, C44, C45, C46, C47, C48, C49, C50, C51, C52, C53, C54, C57, C58, C60, C61, C63, C65, C66, C67, C68: 1uF; C_1812_4532Metric
C4, C5, C6, C7, C8, C10, C24, C25, C26, C27, C32, C33, C34, C35, C69, C70: 470uF; CP_Radial_D10.0mm_P5.00mm
C9, C59: 22nF; C_0805_2012Metric
C55, C56: 100nF; C_1210_3225Metric_Pad1.33x2.70mm_HandSolder
D1: TVS_UNIDO-214AC; DO-214AC
D2, D3, D4, D57, D58, D63: SMD-DIODE-100V-200MA(SOD-123); D_SOD-123
D5, D6, D7, D8, D9, D10, D11, D12, D13, D14, D15, D16, D17, D18, D19, D20, D21, D22, D23, D24, D25, D26, D27, D28, D29, D30, D31, D32, D33, D34, D35, D36, D37, D38, D39, D40, D41, D42, D43, D44, D45, D46, D64: FSV20150V; TO-277A
D47, D48, D49, D50, D51, D52, D53, D54, D55, D56, D59, D60, D61, D62: 1N4148WS; D_SOD-323
J1: HEADER4VALULOK; 4PINVALULOK
J2, J4: HEADER6; 6PINVALULOK
J3: FUSE; AUTO_FUSE
J5: Load; TerminalBlock_Phoenix_MKDS-1,5-2-5.08_1x02_P5.08mm_Horizont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
J7: Vin; TerminalBlock_Phoenix_MKDS-1,5-2-5.08_1x02_P5.08mm_Horizont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
JP1, JP3, JP5, JP7: Jumper; SolderJumper-2_P1.3mm_Open_RoundedPad1.0x1.5mm
JP2, JP4, JP6: Jumper; SolderJumper-2_P1.3mm_Bridged2Bar_RoundedPad1.0x1.5mm
JP8, JP9, JP10: SolderJumper_3_Bridged12; SolderJumper-3_P1.3mm_Bridged2Bar12_RoundedPad1.0x1.5mm
Q1, Q2, Q3, Q4, Q5, Q6, Q7, Q9, Q11: C3M0280090D; TO-247-3_Horizontal_TabDown
R1, R2, R3, R4, R5, R6, R13, R21, R23, R28, R42: 2.2k; R_1206_3216Metric
R7, R8, R10, R11, R12, R33, R34, R35, R36, R37, R38, R39, R40: 47k; R_1206_3216Metric
R9, R30, R31, R32: 0.0005; R_2512_6332Metric_Pad1.40x3.35mm_HandSolder
R14, R15, R16, R17, R18, R19, R44, R46, R48: 10; R_Axial_DIN0411_L9.9mm_D3.6mm_P15.24mm_Horizontal
R20, R22, R25, R41: 192k; R_1206_3216Metric
R24, R26, R27, R29, R43: 1k; R_1206_3216Metric
S1: MOMENTARY-SWITCH-SPST-PTH-6.0MM; TACTILE_SWITCH_PTH_6.0MM
U1: Raspberry Pi Pico; RPi_Pico_SMD_TH
U2, U13, U14, U15: INA181; SOT23-6
U3: V_REG_78XX; V78W_BACKWARDS
U4: TC1240A; SOT23-6
U5, U6, U7, U19, U20, U21: DGD2304; SOIC-8_3.9x4.9mm_P1.27mm
U8, U9: ISO7760FQDWRQ1; SOIC-16W_7.5x10.3mm_P1.27mm
U10, U12, U16: OPA2376AIDR; D8
U11: ADC108S022CIMTX/NOPB; MTC16
U$1: COIL_A+; PAD
U$2, U$3, U$4, U$5, U$6, U$7, U$8: PAD

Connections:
3.3V: C17.1, C40.1, C43.1, C44.1, C45.1, C48.1, C50.1, C52.1, C54.1, C55.1, C56.1, C63.1, R10.2, R33.2, R35.2, R37.2, U1.36 (3V3), U2.6 (VCC), U8.1 (Vcc1), U9.16 (Vcc2), U10.8 (V+), U11.2 (VA), U11.13 (VD), U12.8 (V+), U13.6 (VCC), U14.6 (VCC), U15.6 (VCC), U16.8 (V+)
5V: C11.1, C12.1, C57.1, C58.1, C60.2, D49.1 (K), D52.1 (K), D55.1 (K), D59.1 (K), D61.1 (K), J1.2, J2.2, J4.2, R1.2, R2.2, R3.2, U1.39 (VSYS), U3.OUT, U4.1 (VIN), U8.16 (Vcc2), U9.1 (Vcc1)
/10V: C15.1, C16.1, D2.2 (A), D3.2 (A), D4.2 (A), D57.2 (A), D58.2 (A), D63.2 (A), U4.5 (VOUT), U5.3 (VCC), U6.3 (VCC), U7.3 (VCC), U19.3 (VCC), U20.3 (VCC), U21.3 (VCC)
/A_O: U1.21 (GPIO16), U8.7 (INF)
/Analog_IO/VSENSE_A_IN: C41.1, D47.1 (K), D61.2 (A), D62.1 (K), R21.2, R27.1
/Analog_IO/VSENSE_B_IN: C47.1, D51.1 (K), D52.2 (A), D53.1 (K), R28.2, R29.1
/Analog_IO/VSENSE_C_IN: C42.1, D48.1 (K), D49.2 (A), D50.1 (K), R23.2, R24.1
/Analog_IO/VSENSE_L_IN: C61.1, D54.1 (K), D55.2 (A), D56.1 (K), R42.2, R43.1
/B_O: U1.22 (GPIO17), U8.6 (INE)
/CTRL_A: U5.1 (LIN), U5.2 (HIN), U8.10 (OUTF)
/CTRL_B: U6.1 (LIN), U6.2 (HIN), U8.11 (OUTE)
/CTRL_C: U7.1 (LIN), U7.2 (HIN), U8.12 (OUTD)
/CTRL_DA: U8.13 (OUTC), U19.2 (HIN)
/CTRL_DB: U8.14 (OUTB), U20.2 (HIN)
/CTRL_DC: U8.15 (OUTA), U21.2 (HIN)
/C_O: U1.24 (GPIO18), U8.5 (IND)
/DA_O: U1.25 (GPIO19), U8.4 (INC)
/DB_O: U1.26 (GPIO20), U8.3 (INB)
/DCH_A_H: R44.2, U19.7 (HO)
/DCH_B_H: R46.2, U20.7 (HO)
/DCH_C_H: R48.2, U21.7 (HO)
/DC_O: U1.27 (GPIO21), U8.2 (INA)
/DRV_AH: R14.2, U5.7 (HO)
/DRV_AL: R15.2, U5.5 (LO)
/DRV_BH: R16.2, U6.7 (HO)
/DRV_BL: R17.2, U6.5 (LO)
/DRV_CH: R18.2, U7.7 (HO)
/DRV_CL: R19.2, U7.5 (LO)
/HA_I: U1.17 (GPIO13), U9.12 (OUTD)
/HB_I: U1.19 (GPIO14), U9.11 (OUTE)
/HC_I: U1.20 (GPIO15), U9.10 (OUTF)
CAP_BANK_A+: C10.1, C23.1, D5.1 (A), D5.2 (A), D6.1 (A), D6.2 (A), D9.1 (A), D9.2 (A), D16.1 (A), D16.2 (A), D17.1 (A), D17.2 (A), D18.1 (A), D18.2 (A), JP2.2 (B), Q2.2 (D), Q7.2 (D), R20.2
CAP_BANK_B+: C27.1, C30.1, D19.1 (A), D19.2 (A), D26.1 (A), D26.2 (A), D27.1 (A), D27.2 (A), D28.1 (A), D28.2 (A), D39.1 (A), D39.2 (A), D41.1 (A), D41.2 (A), JP4.2 (B), Q3.2 (D), Q9.2 (D), R25.2
CAP_BANK_C+: C35.1, C38.1, D29.1 (A), D29.2 (A), D36.1 (A), D36.2 (A), D37.1 (A), D37.2 (A), D38.1 (A), D38.2 (A), D43.1 (A), D43.2 (A), D45.1 (A), D45.2 (A), JP6.2 (B), Q5.2 (D), Q11.2 (D), R22.2
CAP_BANK_GND: C41.2, C42.2, C47.2, C48.2, C49.2, C50.2, C51.2, C52.2, C53.2, D7.3 (K), D11.3 (K), D40.3 (K), D42.3 (K), D44.3 (K), D46.3 (K), D50.2 (A), D53.2 (A), D62.2 (A), Q1.3 (S), Q4.3 (S), Q6.3 (S), R9.2, R21.1, R23.1, R28.1, R30.2, R31.2, R32.2, R34.1, R36.1, R38.1, U2.3 (IN+), U5.4 (GND), U6.4 (GND), U7.4 (GND), U13.2 (GND), U13.4 (IN-), U14.2 (GND), U14.4 (IN-), U15.2 (GND), U15.4 (IN-)
COIL_A_+: C3.2, D5.3 (K), D7.1 (A), D7.2 (A), Q2.3 (S), U5.6 (VS), U$1.PAD
COIL_A_-: D9.3 (K), D11.1 (A), D11.2 (A), Q1.2 (D), U$2.PAD
COIL_B_+: C2.2, D39.3 (K), D40.1 (A), D40.2 (A), Q3.3 (S), U6.6 (VS), U$3.PAD
COIL_B_-: D41.3 (K), D42.1 (A), D42.2 (A), Q4.2 (D), U$6.PAD
COIL_C_+: C1.2, D43.3 (K), D44.1 (A), D44.2 (A), Q5.3 (S), U7.6 (VS), U$7.PAD
COIL_C_-: D45.3 (K), D46.1 (A), D46.2 (A), Q6.2 (D), U$8.PAD
DUTY: C59.1, R39.2, R40.2, U11.11 (IN7)
GND: C4.2, C5.2, C11.2, C12.2, C15.2, C16.2, C17.2, C18.2, C19.2, C20.2, C44.2, C45.2, C46.2, C56.2, C57.2, C58.2, C61.2, C68.2, C69.2, C70.2, D1.A, D56.2 (A), D60.2 (A), J2.1, J5.2, J7.2, R9.1, R11.1, R13.1, R42.1, S1.3 (2), U1.3 (GND), U1.8 (GND), U1.13 (GND), U1.18 (GND), U1.23 (GND), U1.28 (GND), U1.38 (GND), U1.42 (GND), U2.2 (GND), U2.4 (IN-), U3.GND, U4.2 (GND), U4.4 (SHDN), U8.8 (GND1), U8.9 (GND2), U9.8 (GND1), U9.9 (GND2), U11.12 (DGND), U19.4 (GND), U20.4 (GND), U21.4 (GND), U$5.PAD
GNDA: C9.2, C40.2, C43.2, C54.2, C55.2, C59.2, C60.1, C63.2, J1.4, J4.1, R7.1, R40.1, U1.33 (AGND), U10.4 (V-), U11.3 (AGND), U12.4 (V-), U16.4 (V-)
HALL_1: J4.5, JP8.1 (A)
HALL_2: J4.4, JP9.1 (A)
HALL_3: J4.3, JP10.1 (A)
HALL_A: R4.2, U9.5 (IND)
HALL_B: R5.2, U9.6 (INE)
HALL_C: R6.2, U9.7 (INF)
ISENSE: U2.1 (OUT), U11.9 (IN5)
ISENSE_A: JP8.3 (B), U13.1 (OUT)
ISENSE_A_HALL_1: JP8.2 (C), U1.31 (GPIO26_ADC0)
ISENSE_B: JP9.3 (B), U14.1 (OUT)
ISENSE_B_HALL_2: JP9.2 (C), U1.32 (GPIO27_ADC1)
ISENSE_C: JP10.3 (B), U15.1 (OUT)
ISENSE_C_HALL_3: JP10.2 (C), U1.34 (GPIO28_ADC2)
LOAD+: C65.2, C66.2, C67.2, C68.1, C69.1, C70.1, D64.3 (K), J5.1, Q7.3 (S), Q9.3 (S), Q11.3 (S), R41.2, U19.6 (VS), U20.6 (VS), U21.6 (VS)
unnamed: C1.1, D2.1 (K), U7.8 (VB)
unnamed: C2.1, D3.1 (K), U6.8 (VB)
unnamed: C3.1, D4.1 (K), U5.8 (VB)
unnamed: C10.2, C23.2, D8.1 (A), D8.2 (A), D13.3 (K), JP1.2 (B)
unnamed: C6.2, C13.2, D10.1 (A), D10.2 (A), D14.3 (K)
unnamed: C7.2, C21.2, D12.1 (A), D12.2 (A), D15.3 (K), JP1.1 (A)
unnamed: C6.1, C13.1, D13.1 (A), D13.2 (A), D16.3 (K)
unnamed: C7.1, C21.1, D14.1 (A), D14.2 (A), D17.3 (K)
unnamed: C8.1, C22.1, D15.1 (A), D15.2 (A), D18.3 (K), JP2.1 (A)
unnamed: C27.2, C30.2, D20.1 (A), D20.2 (A), D23.3 (K), JP3.2 (B)
unnamed: C24.2, C31.2, D21.1 (A), D21.2 (A), D24.3 (K)
unnamed: C25.2, C28.2, D22.1 (A), D22.2 (A), D25.3 (K), JP3.1 (A)
unnamed: C24.1, C31.1, D23.1 (A), D23.2 (A), D26.3 (K)
unnamed: C25.1, C28.1, D24.1 (A), D24.2 (A), D27.3 (K)
unnamed: C26.1, C29.1, D25.1 (A), D25.2 (A), D28.3 (K), JP4.1 (A)
unnamed: C35.2, C38.2, D30.1 (A), D30.2 (A), D33.3 (K), JP5.2 (B)
unnamed: C32.2, C39.2, D31.1 (A), D31.2 (A), D34.3 (K)
unnamed: C33.2, C36.2, D32.1 (A), D32.2 (A), D35.3 (K), JP5.1 (A)
unnamed: C32.1, C39.1, D33.1 (A), D33.2 (A), D36.3 (K)
unnamed: C33.1, C36.1, D34.1 (A), D34.2 (A), D37.3 (K)
unnamed: C34.1, C37.1, D35.1 (A), D35.2 (A), D38.3 (K), JP6.1 (A)
unnamed: D47.2 (A), R20.1
unnamed: D48.2 (A), R22.1
unnamed: D51.2 (A), R25.1
unnamed: D54.2 (A), R41.1
unnamed: C65.1, D57.1 (K), U19.8 (VB)
unnamed: C66.1, D58.1 (K), U20.8 (VB)
unnamed: C67.1, D63.1 (K), U21.8 (VB)
unnamed: J1.1, R39.1
unnamed: J1.3, R8.1
unnamed: J2.3, R3.1, R6.1
unnamed: J2.4, R2.1, R5.1
unnamed: J2.5, R1.1, R4.1
unnamed: J3.1A (1), J3.1B (1), U$4.PAD
unnamed: J7.1, JP7.2 (B), U3.IN
unnamed: Q1.1 (G), R15.1
unnamed: Q2.1 (G), R14.1
unnamed: Q3.1 (G), R16.1
unnamed: Q4.1 (G), R17.1
unnamed: Q5.1 (G), R18.1
unnamed: Q6.1 (G), R19.1
unnamed: Q7.1 (G), R44.1
unnamed: Q9.1 (G), R46.1
unnamed: Q11.1 (G), R48.1
unnamed: S1.1, U1.30 (RUN)
unnamed: C46.1, R10.1, R11.2, U2.5 (REF)
unnamed: C14.2, U4.6 (C+)
unnamed: C14.1, U4.3 (C-)
unnamed: R26.2, U10.3 (+)
unnamed: R27.2, U10.5 (+)
unnamed: R29.2, U12.3 (+)
unnamed: R24.2, U12.5 (+)
unnamed: C49.1, R33.1, R34.2, U13.5 (REF)
unnamed: C51.1, R35.1, R36.2, U14.5 (REF)
unnamed: C53.1, R37.1, R38.2, U15.5 (REF)
unnamed: R43.2, U16.5 (+)
SHUNT_A+: C8.2, C22.2, D8.3 (K), D10.3 (K), D12.3 (K), R30.1, U13.3 (IN+)
SHUNT_B+: C26.2, C29.2, D20.3 (K), D21.3 (K), D22.3 (K), R31.1, U14.3 (IN+)
SHUNT_C+: C34.2, C37.2, D30.3 (K), D31.3 (K), D32.3 (K), R32.1, U15.3 (IN+)
SPI0_CSn: U1.7 (GPIO5), U11.1 (~CS)
SPI0_RX: U1.6 (GPIO4), U11.15 (DOUT)
SPI0_SCK: U1.4 (GPIO2), U11.16 (SCLK)
SPI0_TX: U1.5 (GPIO3), U11.14 (DIN)
THROTTLE: C9.1, R7.2, R8.2, U11.10 (IN6)
VSENSE: U10.1, U10.2 (-), U11.7 (IN3)
VSENSE_A: U10.6 (-), U10.7, U11.4 (IN0)
VSENSE_B: U11.5 (IN1), U12.1, U12.2 (-)
VSENSE_C: U11.6 (IN2), U12.6 (-), U12.7
VSENSE_IN: D59.2 (A), D60.1 (K), R12.1, R13.2, R26.1
VSENSE_L: U11.8 (IN4), U16.6 (-), U16.7
V_RAW: C4.1, C5.1, C18.1, C19.1, C20.1, D1.C, D6.3 (K), D19.3 (K), D29.3 (K), D64.1 (A), D64.2 (A), J3.2A (2), J3.2B (2), JP7.1 (A), R12.2

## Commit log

2024-07-12 Imported board into KiCad and made first version of schematic.
    [BEMF_Controller.kicad_pcb, BEMF_Controller.kicad_sch, Cap_banks.kicad_sch]
2024-07-13 Fixed two errors
    [BEMF_Controller.kicad_sch]
2024-07-13 replaced shottky diodes
    [BEMF_Controller.kicad_sch, Cap_banks.kicad_sch]
2024-07-13 Adapted footprint for capacitors.
    [Cap_banks.kicad_sch]
2024-07-13 Updated schematic pdf
2024-07-13 Detach controller power supply from power section.
    [BEMF_Controller.kicad_sch]
2024-07-13 Added diode and resistors to gate drive for faster switch off
    [BEMF_Controller.kicad_sch]
2024-07-13 Typo. Cap_bank_a label still on driver for bank c
    [BEMF_Controller.kicad_sch]
2024-07-13 Change to mosfets.
    [BEMF_Controller.kicad_sch, Cap_banks.kicad_sch]
2024-07-13 Updated Shottky footprint
    [BEMF_Controller.kicad_sch, Cap_banks.kicad_sch]
2024-07-14 Added component library
    [BEMF_Controller.kicad_pcb, BEMF_Controller.kicad_sch]
2024-07-14 reverted pcb back to original
    [BEMF_Controller.kicad_pcb, BEMF_Controller.kicad_sch]
2024-07-14 Added isolators for digital I/O
    [BEMF_Controller.kicad_sch]
2024-07-14 Added buffers for analog inputs
    [BEMF_Controller.kicad_sch]
2024-07-14 Added few more decoupling capacitors.
    [BEMF_Controller.kicad_sch]
2024-07-14 Referenced ovp circuit to v_shunt+ rather than ground.
    [BEMF_Controller.kicad_sch]
2024-07-14 Added rotor drag
2024-07-15 Added external spi ADC for current and voltage sense per bridge
    [BEMF_Controller.kicad_sch, Cap_banks.kicad_sch]
2024-07-16 Forgot to add new sheets
    [Analog_IO.kicad_sch, Current_sense.kicad_sch]
2024-07-16 Several updates to analog section
    [Analog_IO.kicad_sch, BEMF_Controller.kicad_sch, Cap_banks.kicad_sch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]
2024-07-16 Further work on a/o current sensing circuits.
    [BEMF_Controller.kicad_pcb, BEMF_Controller.kicad_sch, Current_sense.kicad_sch]
2024-07-18 Added hall sensor doc
2024-07-20 Added Kicad model for mosfet.
2024-07-20 Changed footprint for Mosfet. Needs more work.
    [BEMF_Controller.kicad_pcb, BEMF_Controller.kicad_sch]
2024-07-20 Some further work on pcb
    [BEMF_Controller.kicad_pcb]
2024-07-27 First version of PCB layout.
    [Analog_IO.kicad_sch, BEMF_Controller.kicad_pcb, BEMF_Controller.kicad_sch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]
2024-07-29 Feature complete, zero eroors in pcb. Still lot of warnings.
    [Analog_IO.kicad_sch, BEMF_Controller.kicad_pcb, BEMF_Controller.kicad_sch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]
2024-07-30 Added analog Hall inputs and worked away lot of warnings.
    [Analog_IO.kicad_sch, BEMF_Controller.kicad_pcb, BEMF_Controller.kicad_sch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]
2024-07-31 Simplification, high and low side driven together.
    [Analog_IO.kicad_sch, BEMF_Controller.kicad_pcb, BEMF_Controller.kicad_sch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]
2024-07-31 Fixed all warnings.
    [Analog_IO.kicad_sch, BEMF_Controller.kicad_pcb, BEMF_Controller.kicad_sch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]
2024-09-12 Change of plans. Make simple controller for MEG only
    [Analog_IO.kicad_sch, BEMF_Controller.kicad_pcb, Cap_banks.kicad_sch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]
2024-10-09 Finished buck converter schematic
    [MEG_Controller.kicad_pcb, MEG_Controller.kicad_sch]
2024-10-17 Updated gate drivers.
    [MEG_Controller.kicad_pcb, MEG_Controller.kicad_sch]
2024-10-18 Forgot to add some footprints.
2024-10-20 Pretty much complete, but a few things left to do.
    [Analog_IO.kicad_sch, MEG_Controller.kicad_pcb, MEG_Controller.kicad_sch]
